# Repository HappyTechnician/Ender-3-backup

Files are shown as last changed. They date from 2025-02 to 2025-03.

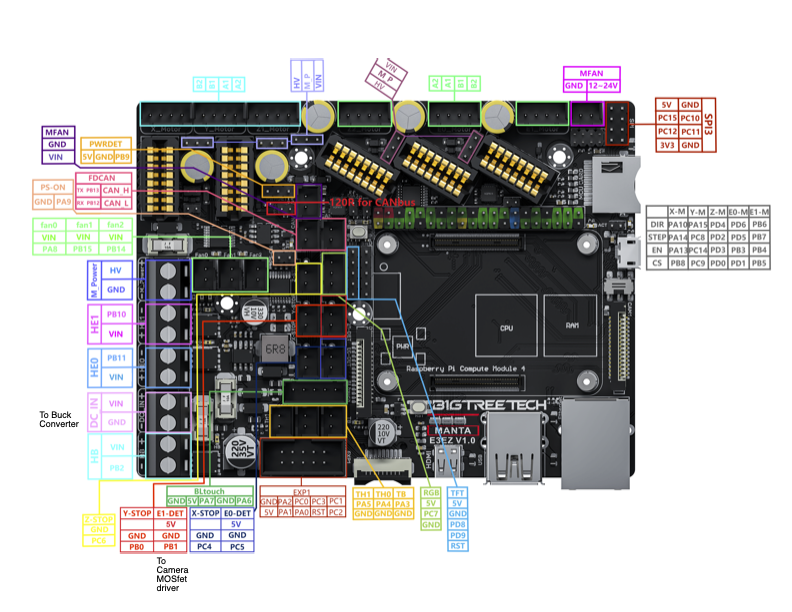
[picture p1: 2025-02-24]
Pics_parts_pinouts/ Manta E3EZ V1.0-PINOUT.png

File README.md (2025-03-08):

# Ender-3-backup
A backup of the configuration files for my Ender-3 printer.
The printer is enclosed in an 1/4" acrylic chamber 24" x 24" x 36" =0.914 m 12'^
A 1000 Watt PTC heater with a Noctua 140mm hv fan heats chamber.
the printer uses LDO high temp stepper motors on all axis.
A BTT Manta E3EZ controller with a CM4-EMMC operate the printer,
along with a Rpi Pico-2350 that monitors the chamber temprature sensors.
A Sprite direct drive extruder with a CR-Touch controls the fillament.
A Fillament sensor is attached to the top cross member.

** UPDATE **
I tried to use a Rpi-pico2 2350 communicating via UART.
THIS WAS AN EPIC FAILURE. After six trial and fails, I resorted to 
USB as the best and easiest configuration for this device.

I followed: https://Github/Rootiest/guides/usb-pico.md 
ALSO: The MAX31855 sensor and the BME280 sensor have a tendency to
throw KNACK ERROR's and shutdown the MCU.
Therefore we will not be using those sensor in this build..

The MANTA E3EZ has a thermister and heater output for a second extruder,
we will be using them for the chamber heater...

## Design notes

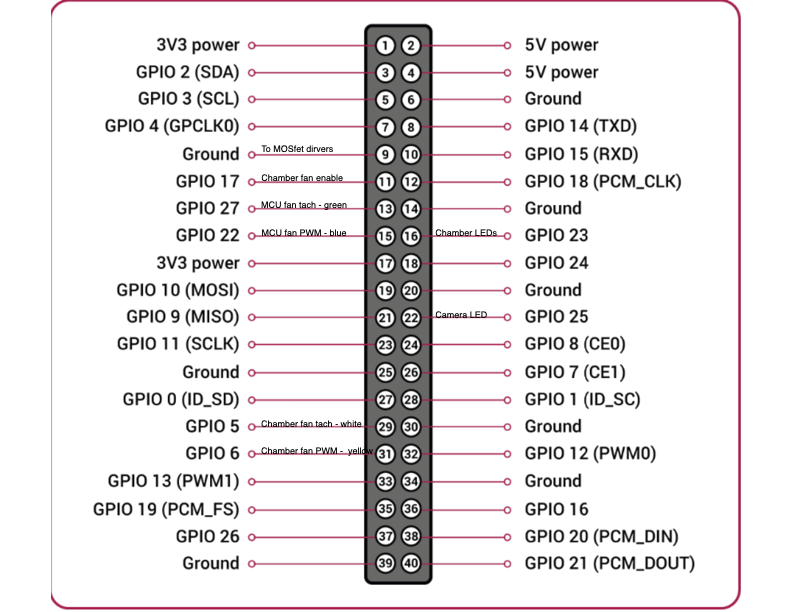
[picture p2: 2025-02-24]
Pics_parts_pinouts/CM-4 pinout.png

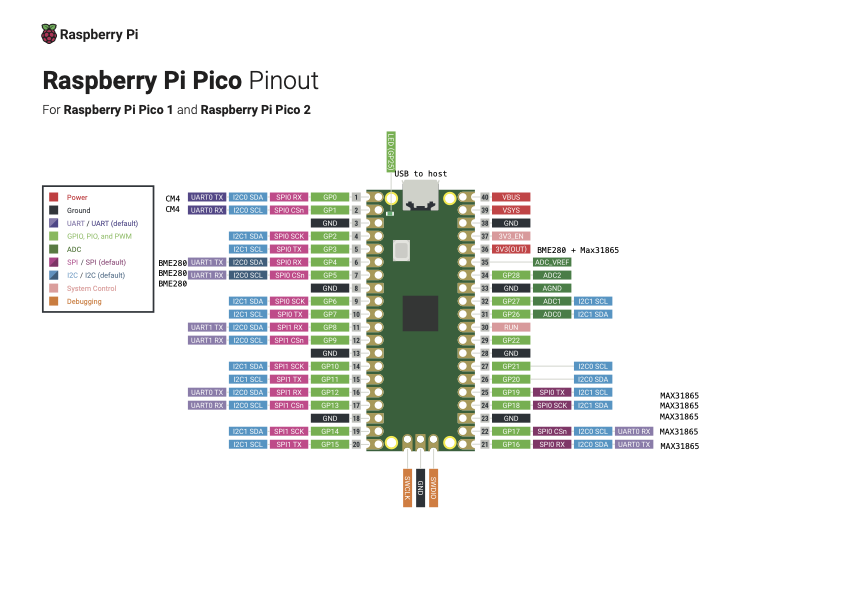
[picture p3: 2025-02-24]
Pics_parts_pinouts/Pico-2-Pinout.png

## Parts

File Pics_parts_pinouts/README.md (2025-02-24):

These files are .jpg .pdf. or .stl for pics, parts,and pinouts.
There are some Thingaverse files I have posted there, along with
parts I have DL'd from there.

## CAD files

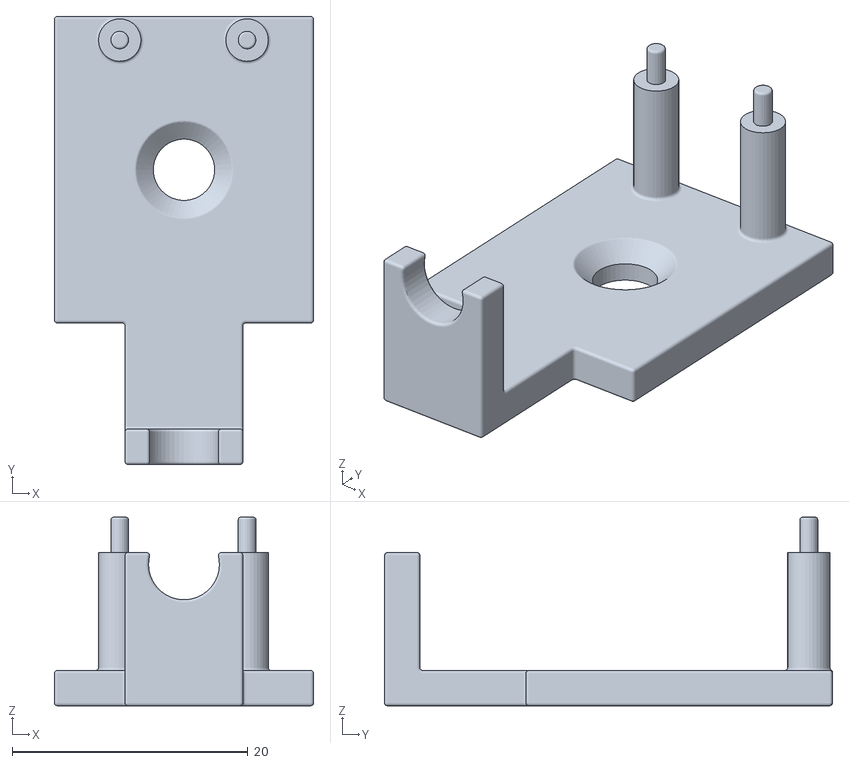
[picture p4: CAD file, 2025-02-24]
Pics_parts_pinouts/BME680 mount bracket v3.stl
22.0 x 38.0 x 16.0

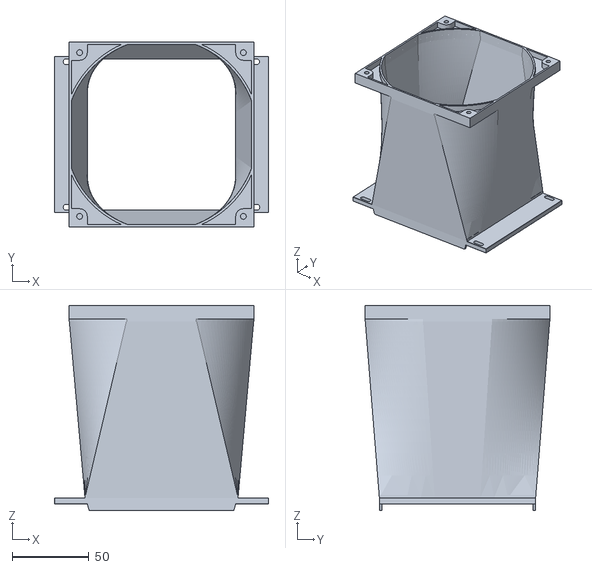
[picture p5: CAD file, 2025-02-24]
Pics_parts_pinouts/1000Watt heater with 120mm fan v1.stl
139.0 x 120.0 x 133.3

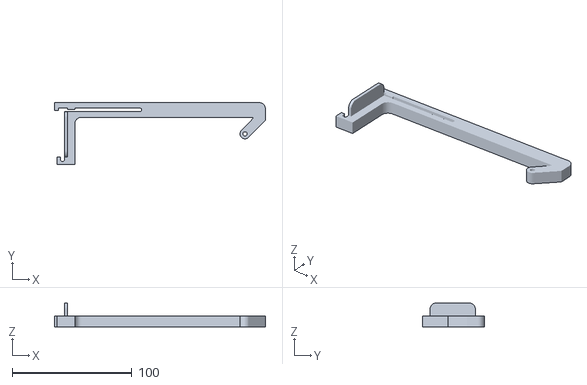
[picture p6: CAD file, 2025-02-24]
Pics_parts_pinouts/Modified_E3_Camera_Mount v2.stl
176.1 x 51.7 x 20.0

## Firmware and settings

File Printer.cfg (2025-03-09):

### Printer configuration for Ender 3 V2, Modified into an S1 PRO.
### including a 110vac heated bed, 110vac heated chamber, LED chamber lights,
### RGB-LEDhead strip, S1 Extruder... 
### Using a CM4_4gb Pi (host), Rpi-pico 2350 auxilary mcu (pico),
### Printer MCU is BTT Manta E3EZ...
# See docs/Config_Reference.md for a description of parameters.

[mcu]   ## E3EZ
serial: /dev/serial/by-id/usb-Klipper_stm32g0b1xx_2C0017000A504B5735313920-if00
restart_method: command

[mcu host]   ## R-pi
serial: /tmp/klipper_host_mcu


[mcu pico]  ## R-pi Pico 2040
serial: /dev/serial/by-id/usb-Klipper_rp2040_E6614103E7617721-if00

        

## sensor for E3EZ 
[temperature_sensor E3EZ_temp]
sensor_type: temperature_mcu
sensor_mcu: mcu

## sensor for R-pi
[temperature_sensor host_temp]
sensor_type: temperature_host
sensor_path: /sys/class/thermal/thermal_zone0/temp


[temperature_sensor pico_temp]
sensor_type: temperature_mcu
sensor_mcu: pico


[temperature_fan host_fan]
pin: host: gpio27      # the fan control pin (must be a mosfet or a pwm fan)
max_power: 1.0
shutdown_speed: 0.0
cycle_time: 0.000004
hardware_pwm: False
kick_start_time: 1.0
off_below: 0.3
tachometer_pin: ^host: gpio22
tachometer_ppr: 2
tachometer_poll_interval: 0.0004
sensor_path: /sys/class/thermal/thermal_zone0/temp
sensor_type: temperature_host           # same as a temp_sensor
control: watermark       # the type of hysteresis we are using
max_delta: 2.0            # fan turns on/off at 3° over/under target_temp
max_temp: 80             # just the valid temperature ranges
min_temp: 5
#target_temp: 28.0 
gcode_id: CM4 temp




[printer]
kinematics: cartesian
max_velocity: 500
max_accel: 4000
square_corner_velocity: 7
max_z_velocity: 25
max_z_accel: 30


[bltouch]
sensor_pin: PA6
control_pin: PA7
x_offset: -31.8
y_offset: -40.5
#z_offset:  0.0
probe_with_touch_mode: true
stow_on_each_sample: false

#[output_pin PS_ON]
#pin: PA9

#[output_pin pb9_pin]
#pin: PB9

[neopixel my_neopixel]
pin: PC7
chain_count: 7
color_order: GRB
initial_RED: 0.3
initial_GREEN: 0.0
initial_BLUE: 0.6



[include mainsail.cfg]
[include timelapse.cfg]
[include kinematics.cfg]
[include Pico.cfg]
[include chamber.cfg]
#[include Amacros.cfg]
[include led_progress.cfg]

[firmware_retraction]
retract_length: 0.4
retract_speed: 40

[pause_resume]
recover_velocity: 50

[respond]
default_type: echo

# Enable object exclusion
[exclude_object]

# Enable arcs support
[gcode_arcs]
resolution: 0.1


[bed_screws]
screw1: 30.5, 37
screw2: 30.5, 207
screw3: 204.5, 207
screw4: 204.5, 37

[bed_mesh]
speed: 45
horizontal_move_z: 5
mesh_min: 10, 10
mesh_max: 180, 180
probe_count: 6,6
algorithm: bicubic
fade_start: 1
fade_end: 10
fade_target: 0

[safe_z_home]
home_xy_position: 115, 115
speed: 35
z_hop: 10
z_hop_speed: 15
move_to_previous: False




[filament_switch_sensor material_0]
switch_pin: PC5
pause_on_runout: true
runout_gcode: PAUSE


##########################################################################
###  PINS USED BY CHAMBER HEATER AND FAN                               ###
##########################################################################

#[extruder1]
#step_pin: PB7             #### NOT USED
#dir_pin: PB6              #### NOT USED
#enable_pin: !PB4          #### NOT USED
#heater_pin: PB10 # HE1    #### USED BY CHAMBER HEATER
#sensor_pin: PA5 # T1      #### USDE BY CHAMBER HEATER

#[filament_switch_sensor material_1]
#switch_pin: PB1           #### NOT USED

[heater_generic Chamber_heater]
control = pid
pid_Kp = 54.931 
pid_ki = 0.776
pid_kd = 972.279
min_temp:0
max_temp:70


[extruder]
control: pid
pid_Kp: 21.637
pid_Ki: 1.323
pid_Kd: 88.443
min_temp: 0
max_temp: 300



#####################################
### ADXL1345 Acceleration Sensor  ###  Uncomment for Acceleration configuring and testing
#####################################
#[adxl345]
#cs_pin: PC15     
#spi_software_miso_pin: PC11
#spi_software_mosi_pin: PC12
#spi_software_sclk_pin: PC10
#####################################

##CHAMBERLIGHT
[output_pin chamberlight]
pin: host: gpio23
pwm: TRUE
value: 0.5
shutdown_value: 0.0
cycle_time: 0.010
scale: 2.5

##CAMERALIGHT
[output_pin camera_light]
pin: host: gpio25
pwm: TRUE
value: 1.0
shutdown_value: 0.0
cycle_time: 0.0010

[heater_bed]
heater_pin: PB2 #HB
sensor_type: EPCOS 100K B57560G104F #Generic 3950
sensor_pin: PA3 #TB
control: pid
# tuned for 110vac hardware with 60 degree Celsius target
pid_Kp: 55.685
pid_Ki: 1.237
pid_Kd: 626.452
min_temp: 0
max_temp: 130

[fan]                                 ## Part cooling fan
pin: PA8
max_power: 1.0
Shutdown_speed: 0.0
cycle_time: 0.010
hardware_pwm: False
kick_start_time: 0.100
off_below: 0.0


[heater_fan heatbreak_cooling_fan]   ## Extruder Fan
pin: PB15
max_power: 1.0
Shutdown_speed: 0.0
cycle_time: 0.010
hardware_pwm: False
kick_start_time: 0.100
off_below: 0.0
heater: extruder
heater_temp: 40.0
Fan_speed: 1.0

[board_pins]
aliases:
    # EXP1 header
    EXP1_1=PC1, EXP1_3=PC3, EXP1_5=PC0, EXP1_7=PA2, EXP1_9=<GND>,
    EXP1_2=PC2,  EXP1_4=<RST>, EXP1_6=PA0, EXP1_8=PA1, EXP1_10=<5V>

[display]
lcd_type: st7920
cs_pin: EXP1_7
sclk_pin: EXP1_6
sid_pin: EXP1_8
encoder_pins: ^EXP1_5, ^EXP1_3
click_pin: ^!EXP1_2

[output_pin beeper]
pin: EXP1_1


#*# <---------------------- SAVE_CONFIG ---------------------->
#*# DO NOT EDIT THIS BLOCK OR BELOW. The contents are auto-generated.
#*#
#*# [bed_mesh default]
#*# version = 1
#*# points =
#*# 	0.155000, -0.020000, -0.082500, -0.180000, -0.197500, -0.260000
#*# 	0.220000, 0.062500, 0.017500, -0.097500, -0.132500, -0.235000
#*# 	0.225000, 0.097500, 0.040000, -0.090000, -0.117500, -0.195000
#*# 	0.270000, 0.122500, 0.052500, -0.052500, -0.097500, -0.180000
#*# 	0.227500, 0.110000, 0.040000, -0.092500, -0.107500, -0.180000
#*# 	0.315000, 0.182500, 0.095000, -0.037500, -0.090000, -0.167500
#*# x_count = 6
#*# y_count = 6
#*# mesh_x_pps = 2
#*# mesh_y_pps = 2
#*# algo = bicubic
#*# tension = 0.2
#*# min_x = 10.0
#*# max_x = 180.0
#*# min_y = 10.0
#*# max_y = 180.0
#*#
#*# [bltouch]
#*# z_offset = 3.535

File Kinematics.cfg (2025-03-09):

[stepper_x]
step_pin: PA14
dir_pin: !PA10
enable_pin: !PA13
microsteps: 16
rotation_distance: 40
endstop_pin: ^PC4
position_endstop: 0
position_max: 225
homing_speed: 50

[tmc2209 stepper_x]
uart_pin: PB8
#diag_pin: PC4
run_current: 0.800
stealthchop_threshold: 999999

[stepper_y]
step_pin: PC8
dir_pin: !PA15
enable_pin: !PC14
microsteps: 16
rotation_distance: 40
endstop_pin: ^PB0
position_endstop: 0
position_max: 225
homing_speed: 50

[tmc2209 stepper_y]
uart_pin: PC9
#diag_pin: PB0
run_current: 0.800
stealthchop_threshold: 999999

[stepper_z]
step_pin: PD2
dir_pin: !PD4
enable_pin: !PD3
microsteps: 16
rotation_distance: 8
endstop_pin: probe: z_virtual_endstop
position_max: 225
position_min: -5

[tmc2209 stepper_z]
uart_pin: PD0
#diag_pin: PC6
run_current: 0.850
stealthchop_threshold: 999999


[extruder]
max_extrude_only_distance: 105.0
step_pin: PD5
dir_pin: PD6
enable_pin: !PB3
microsteps: 16
gear_ratio: 42:12
rotation_distance: 26.359
nozzle_diameter: 0.400
filament_diameter: 1.750
heater_pin: PB11 #HE0
sensor_type: EPCOS 100K B57560G104F
sensor_pin: PA4 #TH0
################################# Extruder control in "printer.cfg" #######
#control: pid
#pid_Kp: 21.622
#pid_Ki: 1.172
#pid_Kd: 99.731
#min_temp: 0
#max_temp: 300

[tmc2209 extruder]
uart_pin: PD1
run_current: 0.800
stealthchop_threshold: 999999

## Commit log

2025-02-23 Add new configuration files for Ender-3 printer
    [Amacros.cfg]
2025-02-24 Your commit message here
    [1000Watt heater with 120mm fan v1.stl, BME680 mount bracket v3.stl, Modified_E3_Camera_Mount v2.stl]
2025-02-26 Added led_progress.cfg
    [led_progress.cfg]
2025-02-26 Delete Pico-2-Pinout.pdf
    Removed .pdf files
2025-03-04 Updated all files as Klipper updated API
    [Amacros.cfg, Chamber.cfg, Kinematics.cfg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]
2025-03-04 Small changes to 4 files
    [Chamber.cfg, Pico.cfg, Printer.cfg]
2025-03-09 Files changed for Pico accessories"
    [Chamber.cfg, Kinematics.cfg, Pico.cfg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]
